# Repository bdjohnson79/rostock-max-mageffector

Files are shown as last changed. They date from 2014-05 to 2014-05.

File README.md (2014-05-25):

rostock-max-mageffector
=======================

Magnetic effector and arms for Rostock Max v1 printer

Inspired by designs from seemecnc forum users xnaron (the original magarm
developer) and flateric (who keyed me to the Traxxas ball studs)

Designed for an e3d version 5 hotend.  Due to a small error on my part, the
groovemount needs to be on the bottom side of the effector.

**What you need:**

1. 0.375" OD carbon fiber rods - 6x - length at your discretion, as long as all
6 are identical

2. Traxxas ball studs (part number 4933) - they come on 4 packs.  You'll need 3
packages.

3. These parts - 1 effector, 3 cheapskate adapters, 12 rod ends, 1 assembly jig.

4. 0.25" spacers for #6 screws - 6x

5. 6-32 1.5" SHCS - 6x

6. 3/8 diameter x 3/8 length rare-earth magnets.  I think mine were N62
strength.

**Tools:**

* Thread taps - M5 and 6-32

* Metric allen key (2.5mm) for ball studs

* Standard allen key (7/64) for SHCS

**Printing:**

1. Material: not PLA - these are close to your hot end.  I did ABS.

2. Print setup: I did 0.2mm layers and 50% infill for the effector and
cheapskate adapters.  The rod ends, just print solid.  They're small enough that
infill is irrelevant.

**Assembly:**

1. Tap the M5 holes through the effector and cheapskate adapters, then drive the
ball studs.  Leave enough clearance that a rod end can be completely vertical
without hitting the effector.

2. Use two of the cheapskate adapters plus the assembly jig to ensure all of
your arms are exactly identical in length.  If not, you'll have a hard time
getting good prints.

3. Tap your cheapskates for the #6 screws used for the end stops.  Install the
new parts, and proceed to recalibration.  You'll need to adjust your delta arm
length parameter and printer radius parameter in your firmware.

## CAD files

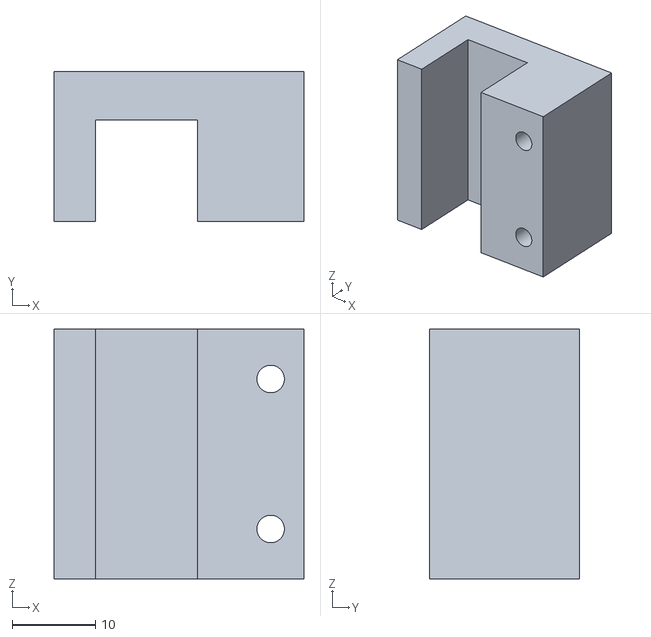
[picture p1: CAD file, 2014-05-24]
assembly_jig.stl
30.0 x 18.0 x 30.0

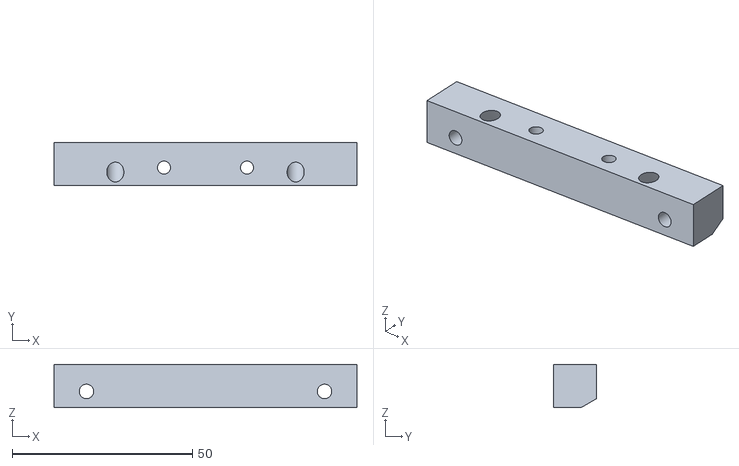
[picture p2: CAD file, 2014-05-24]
cheapskate_adapter.stl
84.0 x 12.0 x 12.0

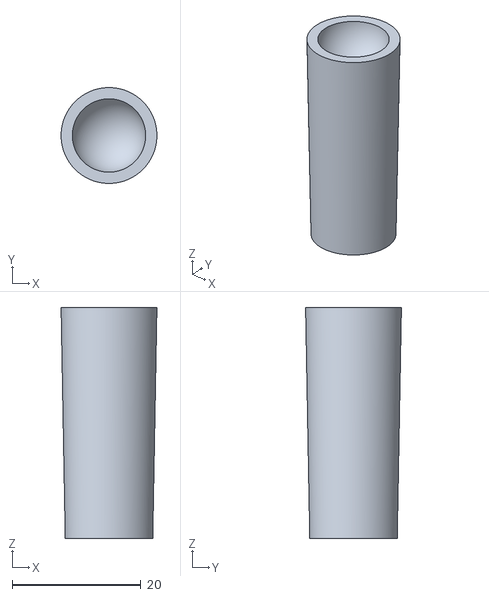
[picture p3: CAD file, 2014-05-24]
rod_end.stl
14.9 x 14.9 x 35.9
